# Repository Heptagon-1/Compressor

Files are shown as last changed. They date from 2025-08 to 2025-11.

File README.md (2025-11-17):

# Compressor: Open Source Compound Bow Press
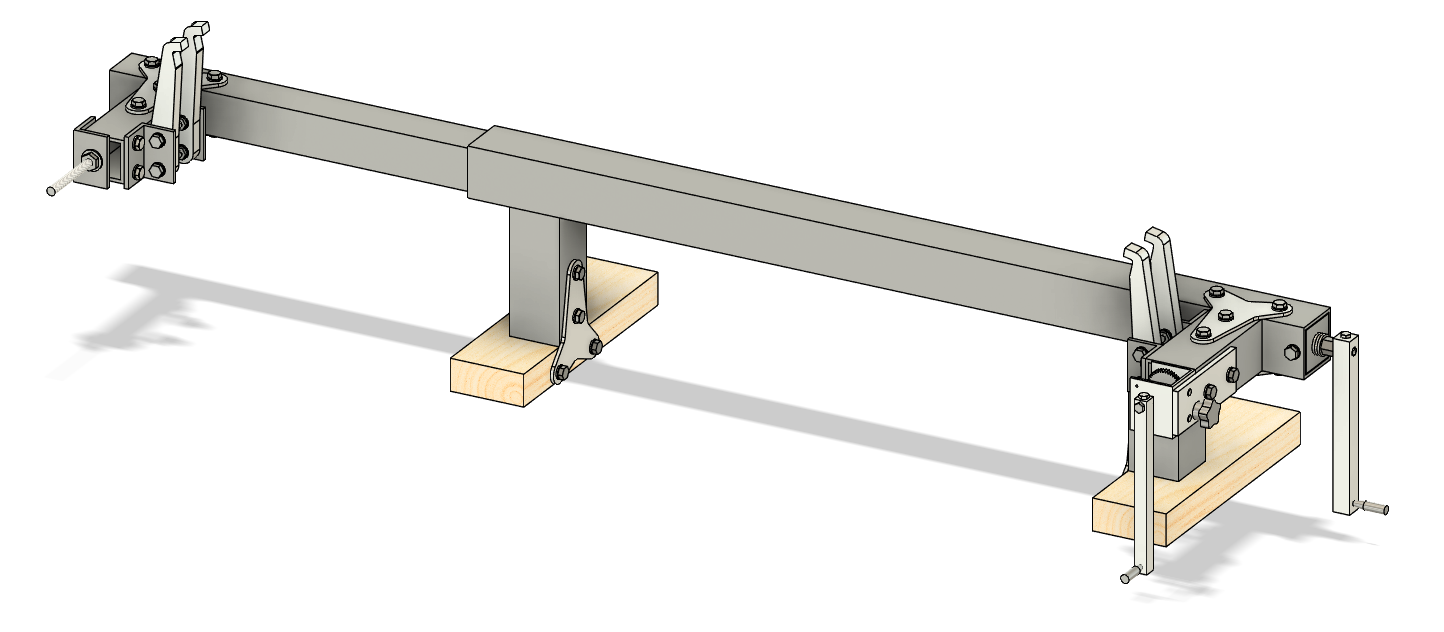
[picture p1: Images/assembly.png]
Assembly


Compressor is a low-cost, highly capable open-source bow press designed to be constructed from commonly available steel and aluminium stock. 
## Features:
- Capable of pressing bows up to 42" AtA.
- Draw board with lock for handsfree use.
- Accommodates split limb bows with a limb gap of more than 12mm (not compatible with past-parallel limbs).
- Parts cost of approximately £250-300.
- No welding required - built entirely using common hand tools.
- Only two custom-made parts - everything else is fabricated from common stock sizes.

## Bill of Materials
⚠️ This list may not be perfect - it is recommended to order a few extra fasteners just in case. 
### Fasteners and Hardware
| Fastener 	| Quantity 	| Notes 	|
|---	|---	|---	|
| M5 nylock nut 	| 4 	| 	|
| M5x22 hex bolt 	| 4 	| 	|
| M5x9 washer 	| 8 	| **Must be reduced diameter 9mm washer (DIN 433).** 	|
| 	| 	| 	|
| M6 nylock nut 	| 1 	| 	|
| M6 washer 	| 3 	| 	|
| M6x10 hex bolt 	| 1 	| 	|
| M6x22 hex bolt 	| 1 	| 	|
| M6x35 star knob 	| 1 	| [Example](https://www.accu.co.uk/threaded-clamping-knobs/588655-HHW-M6-40-35-2-PA) 	|
| M6x85 plain hex bolt 	| 1 	| Plain hex bolt, **not** full threaded. Unthreaded section ~67mm required. 	|
| M6 free-spinning handle 	| 2 	| [Example](https://www.vital-parts.co.uk/m6-x-15mm-x-55mm-rotating-nylon--bzp-cylindrical-threaded-handle---male-40202-p.asp). Alternatively this can be 3D printed, in which case an additional M6x70 plain **socket-head** bolt and m6x22 hex bolt will be required for each handle. STL is available [here](/Manufacturing%20files/Rotating_handle.stl). If buying them, ensure at the thread length is at least 10mm. 	|
| 	| 	| 	|
| M8 thin nut 	| 4 	| 	|
| M8 washer 	| 64 	| 	|
| M8x10 hex bolt 	| 30 	| 	|
| M8x12 hex bolt 	| 14 	| 	|
| M8x30 hex bolt 	| 8 	| 	|
| M8x50 flat point grub screw 	| 2 	| Flat point is important. Get slotted drive rather than hex if possible. 	|
| 8x50mm coach screw 	| 4 	| 	|
| 	| 	| 	|
| M10 thin nut 	| 1 	| 	|
| M10 washer 	| 2 	| 	|
| M10x100 hex bolt 	| 1 	| Must be full threaded **not** plain. 	|
| 	| 	| 	|
| TR10x2 1000mm leadscrew 	| 1 	| Should be right-hand thread, 2mm lead. 	|
| TR10x2 flanged brass leadscrew nut 	| 1 	| Right hand thread, 2mm lead. Check it matches the leadscrew thread. 	|
| TR10x2 steel hex leadscrew nut 	| 2 	| Same as above. 	|
### Raw Materials
#### Steel
Steel box sections formed by extrusion often have a seam that protrudes into the inside of the tube, and is impossible to remove without specialised tools. Check with your supplier that this seam is not so prominent that the 50mm square section cannot comfortably fit inside of the 60mm section otherwise you **will not be able to assemble the press**. 
| Stock type 	| Dimensions 	| Quantity 	| Notes 	|
|---	|---	|---	|---	|
| Square box section 	| 60x60mm, 4mm thickness, 1000mm length 	| 1 	| 	|
| 	| 60x60mm, 4mm thickness, 149mm length  	| 3 	| 	|
| 	| 	| 	| 	|
| 	| 50x50mm, 4mm thickness, 480mm length  	| 1 	| 	|
| 	| 50x50mm, 4mm thickness, 154mm 	| 1 	| 	|
| 	| 	| 	| 	|
| Equal angle 90° section 	| 40x40, 5mm thickness, 60mm length 	| 5 	| 	|
| 	| 	| 	| 	|
| C-channel 	| 50x50mm, 3mm thickness, 50mm length 	| 1 	| 	|
| 	| 40x40mm, 3mm thickness, 40mm length 	| 1 	| 	|
#### Aluminium
| Stock type 	| Dimensions 	| Quantity 	| Notes 	|
|---	|---	|---	|---	|
| Flat bar 	| 2" x 1/4", length = ~130mm 	| 1 	| Steel is sold in metric but a lot of aluminium still seems to be imperial for some reason. 	|
| 	| 	| 	| 	|
| C-channel  	| 2" x 2" x 1/8", length = 60mm 	| 1 	| 	|
| 	| 	| 	| 	|
| Square bar 	| 15x15mm, length=200mm 	| 1 	| 	|
| 	| 20x20mm, length=200mm 	| 1 	| 	|
### Custom Manufactured Parts
These are the only parts of the project that need to be custom-made. Various CNC and waterjet companies are available - if you shop around you should be able to get them made for approximately £100. I have had good experiences with Xometry. A referral link to sign up is available [here](https://get.xometry.uk/r/0f2031980c). DXF / STEP files are available in [Manufacturing files](/Manufacturing%20files).
| Part 	| Quantity 	| CAD File 	| Notes 	|
|---	|---	|---	|---	|
| T-bracket 	| 8 	| [Here](/Manufacturing%20files/T%20Bracket.dxf)	| 4mm thickness. Any aluminium grade. 	|
| Limb finger 	| 4 	| [Here](/Manufacturing%20files/Finger.step)	| Any aluminium grade. 	|
### Other
| Part 	| Quantity 	| Notes 	| 	|
|---	|---	|---	|---	|
| Carabiner 	| 1 	| Ensure this is load-rated for at least the poundage of your bow, ideally at least 3x for safety. 	| 	|
| Paracord 	| 1000mm 	| For the draw board - ensure the strength is sufficient for your bow. 	| 	|
| 40 tooth Mod1 6mm bore gear 	| 1 	| [Example](https://www.gearsandsprockets.co.uk/mod-1-40-tooth-tbot-steel-model-gear.html). Ensure your gear has set screws to clamp to the shaft, or be prepared to drill and tap them. 	| 	|
| Electrical tape 	| 	| 	| 	|
| A4 craft foam sheet 	| 	| 	| 	|
| 2" x 4" timber, length = 300mm 	| 2 	| Dimensions are not critical. Wooden feet stop the press from scratching the surface it sits on. 	| 	|
## Tools Used
- Flat file
- Round file
- Hacksaw
- Cordless drill, common drill bit sizes and cutting fluid
	- Drill bit list TBC
- M6 and M8 taps
- Marking out tools
- Adjustable spanner
- Socket set

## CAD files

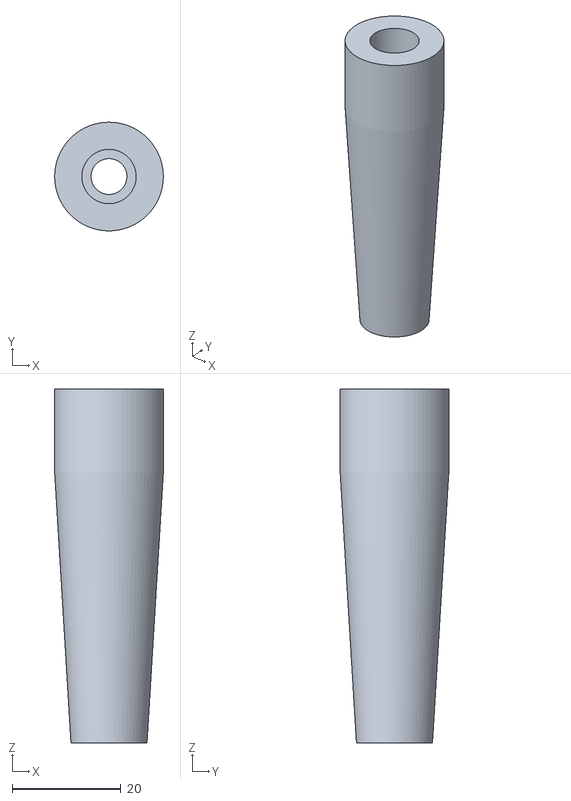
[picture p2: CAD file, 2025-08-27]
Manufacturing files/Rotating_handle.stl
20.0 x 20.0 x 65.1

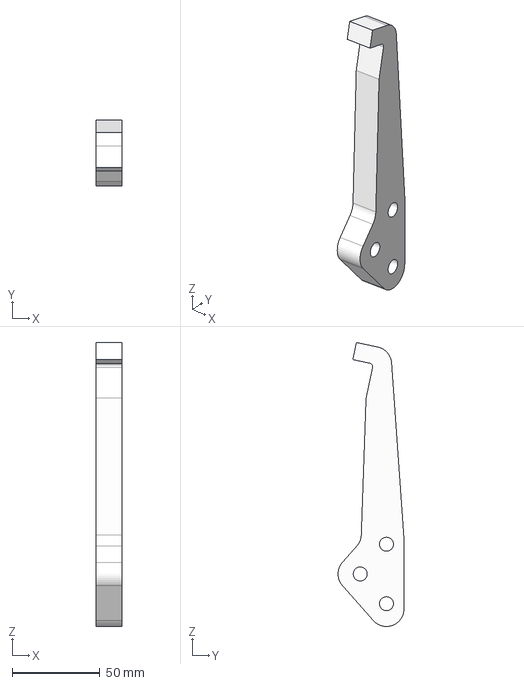
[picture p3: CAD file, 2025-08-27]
Manufacturing files/Finger.step
15.0 x 37.7 x 162.3 mm

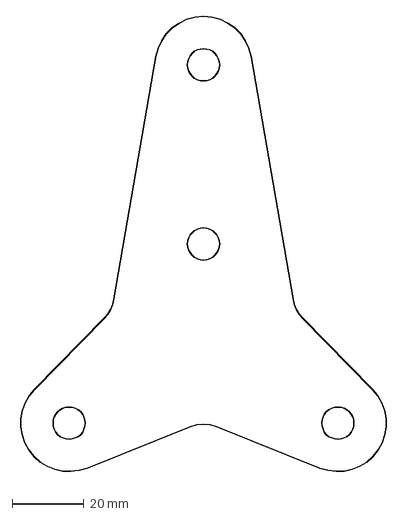
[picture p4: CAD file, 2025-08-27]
Manufacturing files/T Bracket.dxf
104.5 x 128.4 mm

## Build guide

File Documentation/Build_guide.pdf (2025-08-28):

# Build Guide

Some notes before starting:
- This build is designed to be made using hand tools so it doesn’t require any particularly tight tolerances, if everything is within +/-1mm there shouldn’t be any major issues. A couple of areas require slightly finer tolerance than this to make sure things fit together, and these are called out specifically.
- There is quite a lot of drilling and tapping to do in this project. Investing in some decent quality drill bits and cutting fluid will make life a lot easier. I built this using a cordless drill – access to a bench drill isn’t a requirement but will make the build a bit easier.
- If you pick and choose your supplier, you shouldn’t need to cut any big pieces of steel to size yourself as most steel suppliers offer a free or cheap cutting service. The only exception to this were the steel c-channel sections in the leadscrew assembly which are a bit too short for most shops to cut, but these are thin enough that a hacksaw does the job.
- If you have any questions or issues that can’t be resolved using the CAD model then please don’t hesitate to contact me or raise a Github issue.

## 1: Leadscrew Assembly

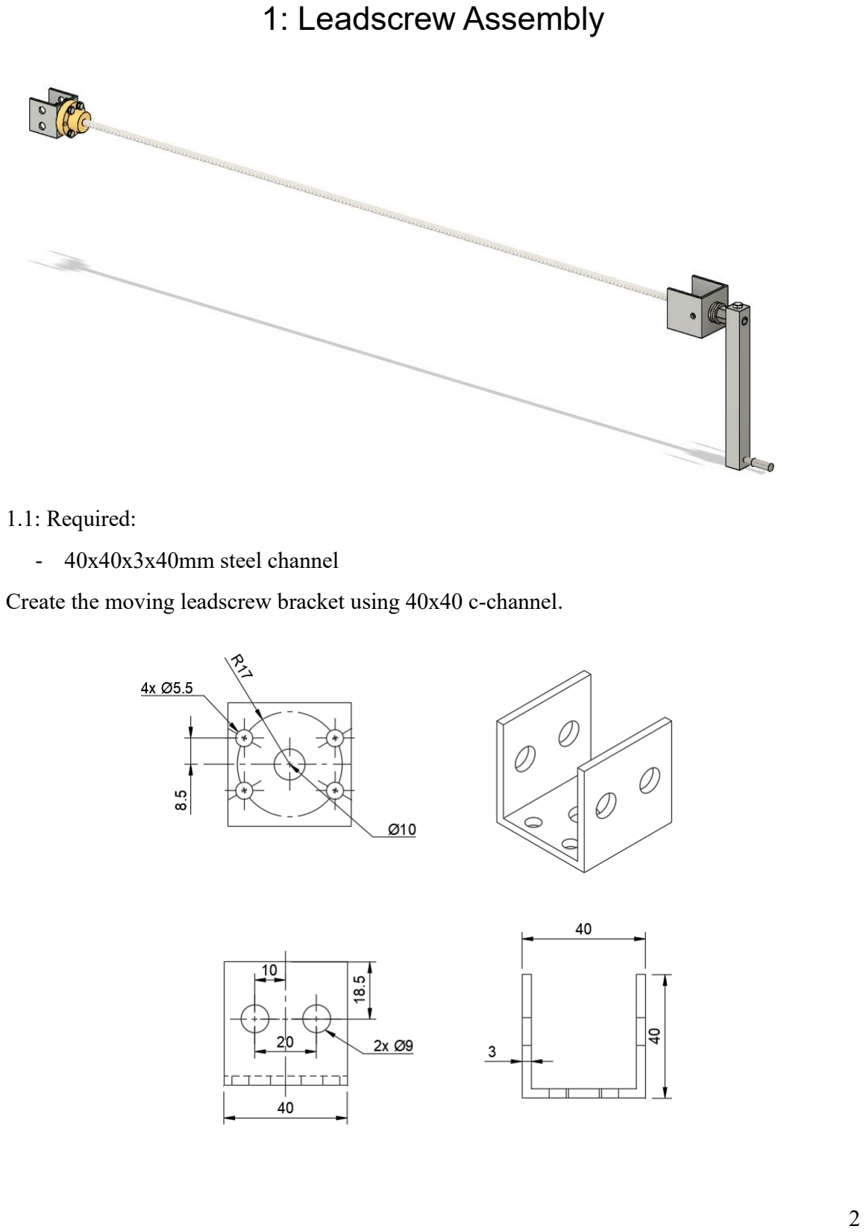
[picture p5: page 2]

1.1: Required:
- 40x40x3x40mm steel channel

Create the moving leadscrew bracket using 40x40 c-channel.

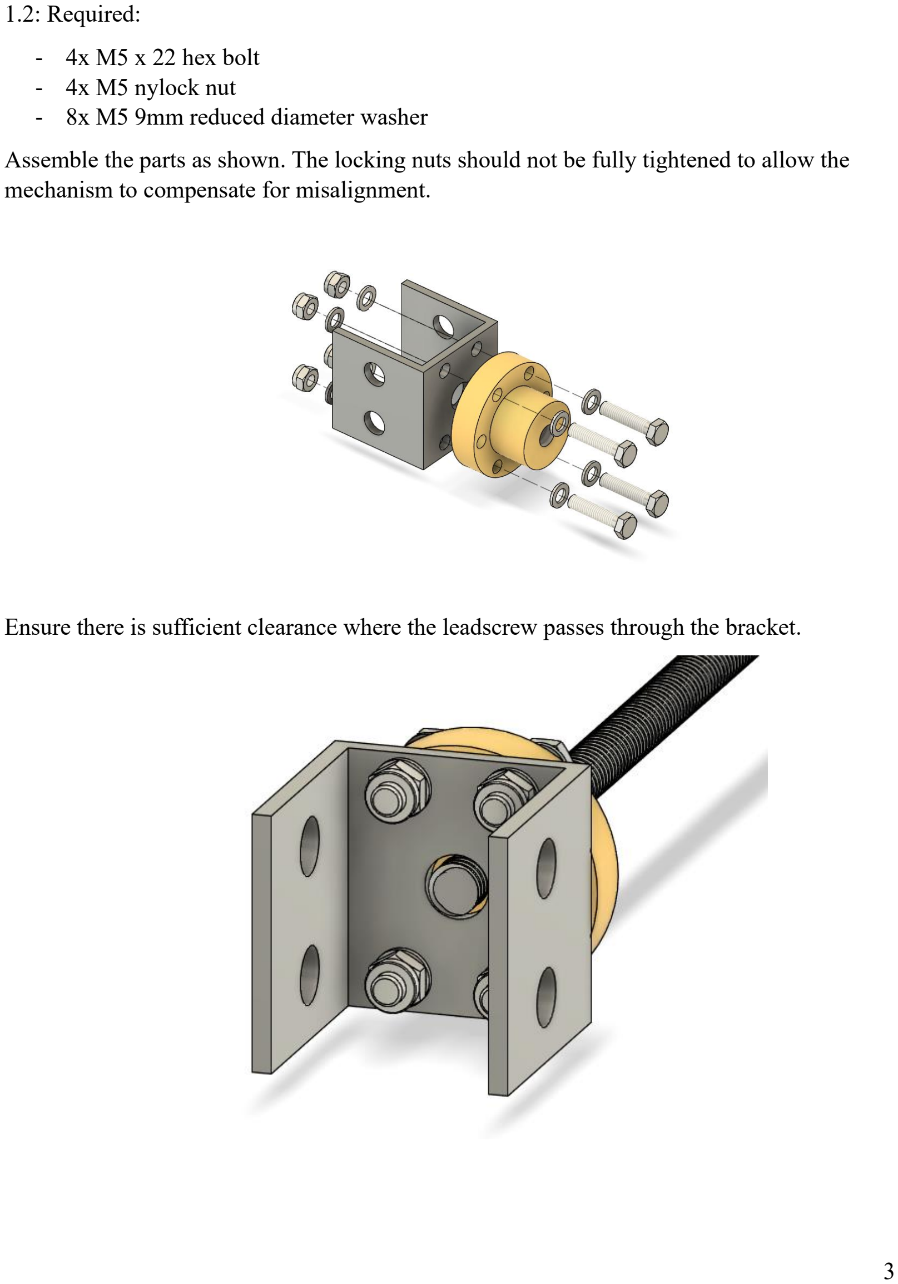
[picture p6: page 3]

1.2: Required:
- 4x M5 x 22 hex bolt
- 4x M5 nylock nut
- 8x M5 9mm reduced diameter washer

Assemble the parts as shown. The locking nuts should not be fully tightened to allow the mechanism to compensate for misalignment.

Ensure there is sufficient clearance where the leadscrew passes through the bracket.

1.3: Required:
- TR10x2 1000mm leadscrew

Prepare the leadscrew by filing a flat on one end. It should extend around 15mm from the end of the screw, and be just deep enough that the threads are not visible in the flat section. Apply some oil to the length of the leadscrew to prevent rust.

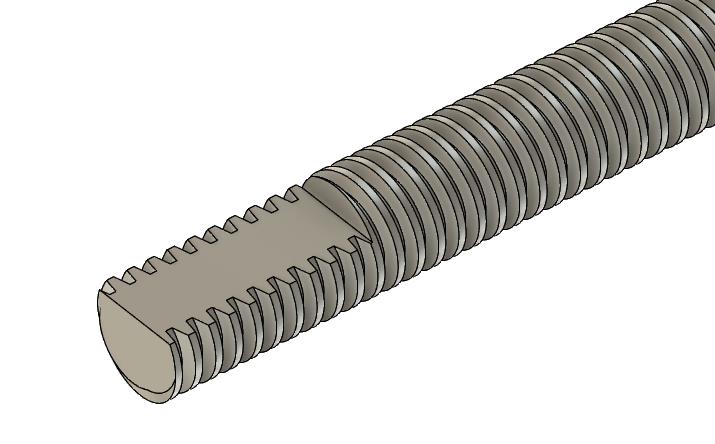
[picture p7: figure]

1.4: Required:
- 20x20x200mm aluminium square bar

Create the handle of the press. If using a 3D printed rotating handle, an additional M6 hole is required on the top. The depth of the threaded holes on the end is not critical so long as they intersect with the holes on the long face.

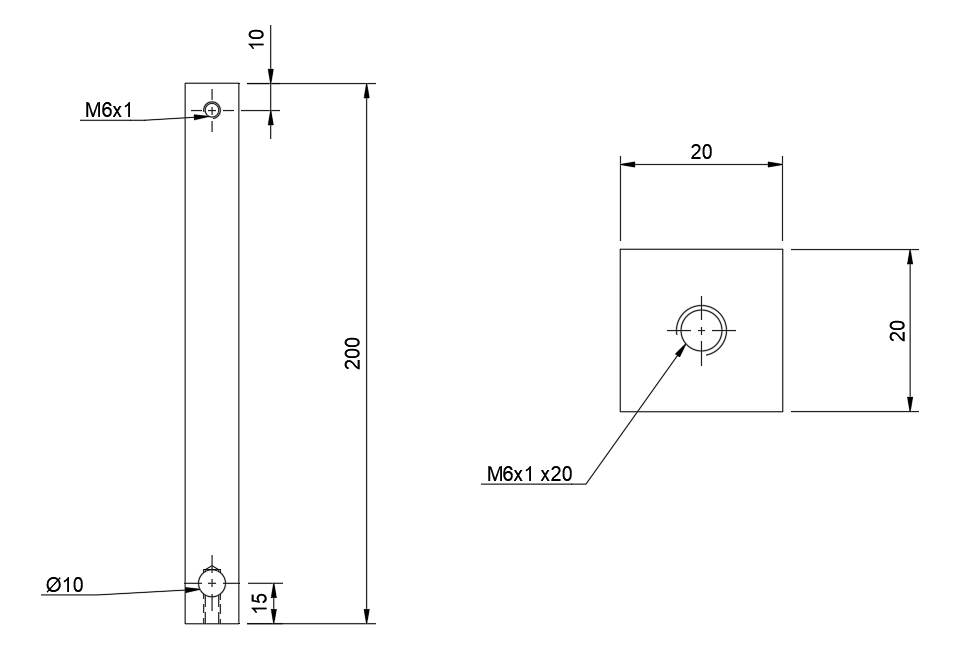
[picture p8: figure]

1.5: Required:
- 50x50x3x50mm steel channel

Create the static leadscrew bracket using the steel channel. Ensure the 10mm hole has sufficient clearance for the leadscrew.

1.6: Required:
- 10mm adjusting ring
- 2x TR10x2 hex leadscrew nut
- 2x 51100 thrust bearing
- Static leadscrew bracket from 1.5
- Leadscrew

Add all of the parts to the leadscrew in the following order:

1. 10mm adjusting ring
2. TR10 hex nut
3. 51100 thrust bearing
4. Static leadscrew bracket
5. 51100 thrust bearing
6. TR10 hex nut

Do not tighten down the adjusting ring yet.

1.7: Required:
- Bow press handle
- M6x22 hex bolt

Attach the handle flush with the end of the leadscrew using the M6 bolt, then move the parts from 1.6 up towards the handle. The bracket should be sandwiched between the two thrust bearings just tightly enough that it cannot rattle. Tighten down the adjusting ring once everything is in place.

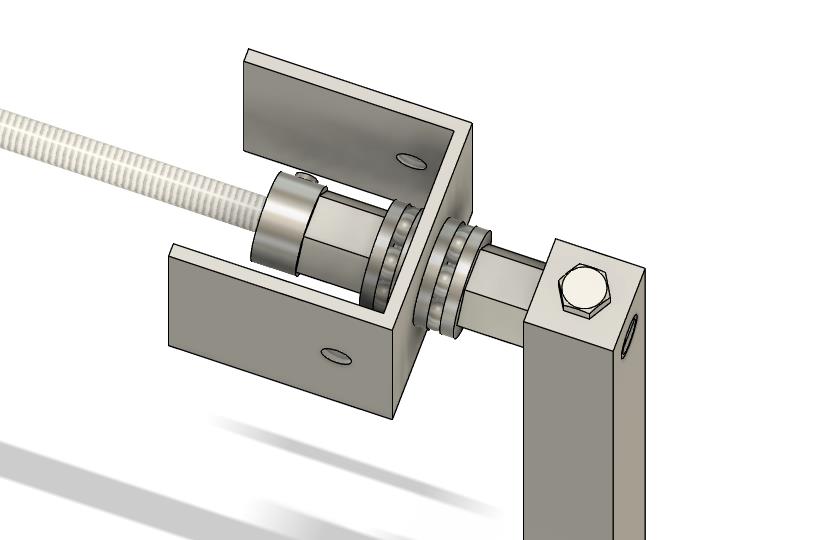
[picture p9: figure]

1.8: Required:
- M6 rotating handle

Attach the free-spinning grip to the end of the handle. If 3D printing the handle instead, lock the bolt in place using the threaded hole you made in the other end.

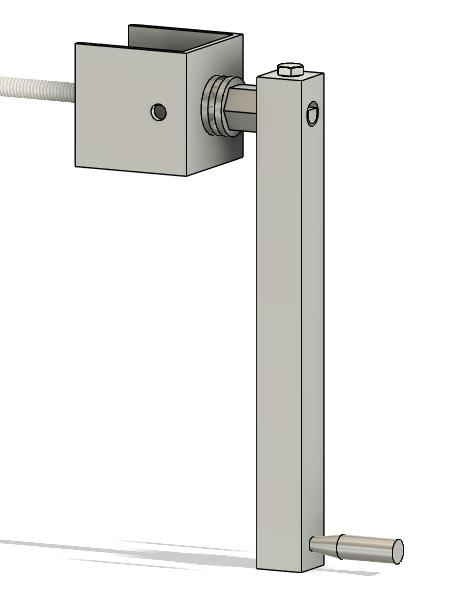
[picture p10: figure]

The leadscrew assembly is now completed.

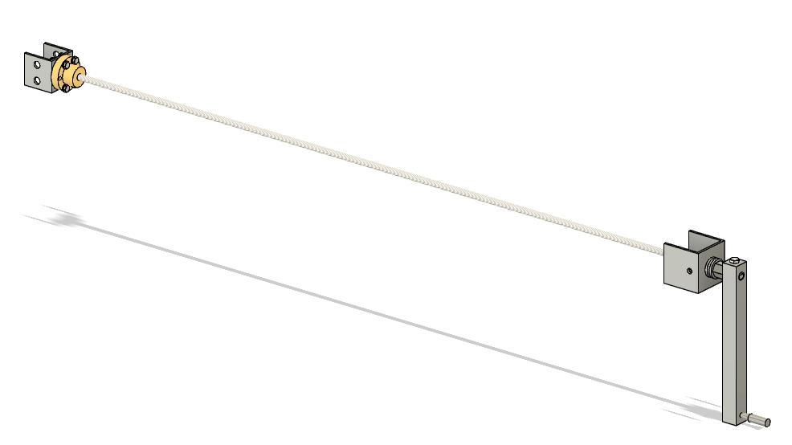
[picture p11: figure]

## 2: Main Mody Assembly

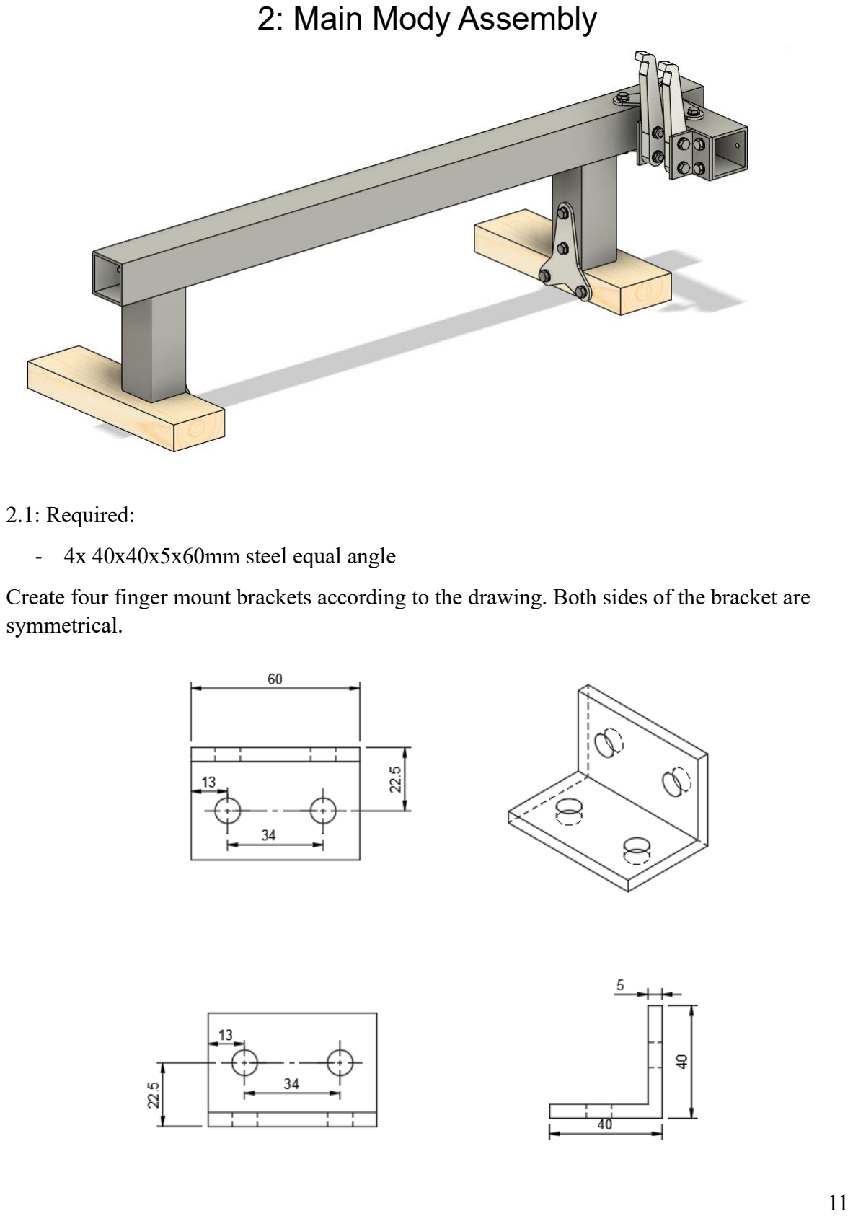
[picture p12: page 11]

2.1: Required:
- 4x 40x40x5x60mm steel equal angle

Create four finger mount brackets according to the drawing. Both sides of the bracket are symmetrical.

2.2: Required:
- 4x Finger mount brackets from 2.1
- 4x Fingers
- 8x M8x30 hex bolts
- 8x M8 thin nuts
- 16x M8 washers

Create four finger assemblies. These are symmetrical – create two left variants and two right variants. Exact alignment of the fingers is not critical right now, this will be adjusted later.

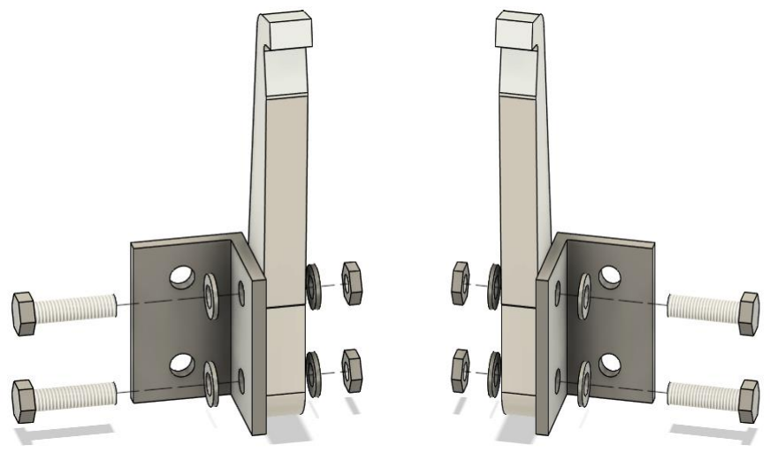
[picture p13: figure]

2.3: Required:
- 60x60x4x1000mm square box section steel

Create the main body of the press. I recommend labelling the top, front, rear and bottom faces of the workpiece first to match the drawings. Note that the hole centreline in the top is 25mm from the front and the line on the rear is 25mm from the bottom. The centreline on the front is in the centre (~30mm from each side). Also note the tolerances on the 25mm dimensions – do not place the holes more than 25mm from the edge, or additional work will be required during assembly

All holes are M8 tapped, except for the 9mm hole through the front and rear faces. Once all hole locations are marked, double check against the drawings and CAD before drilling and tapping any. This is probably the most complex and awkward component in the whole build.

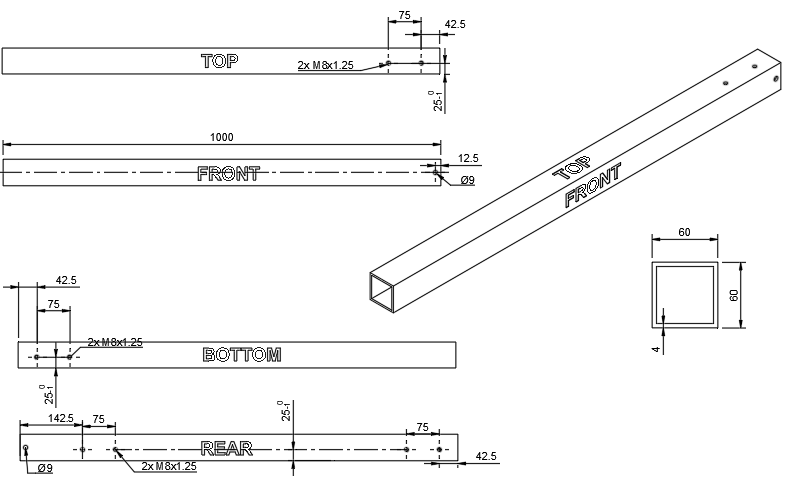
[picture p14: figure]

2.4: Required:
- 2x 60x60x4x149 square box section steel

Create a pair of these which are mirror images. Note the tolerance on the 25mm dimensions. All four holes are M8 tapped.

2.5: Required:
- 60x60x4x149 square box section steel

Create the mount for attaching the fingers. Note the tolerances on some of the dimensions. The distance between the two pairs of holes must be selected to match the gap between your split limbs. The default 107mm value corresponds to PSE Dominator Duo 30mm gap limbs.

Distance between inside limb edges (mm) | Distance value in drawing (mm)
20 | 97
25 | 102
30 (PSE Dominator Duo) | 107

Once the holes are marked, double check against the CAD before drilling. All holes are M8 tapped.

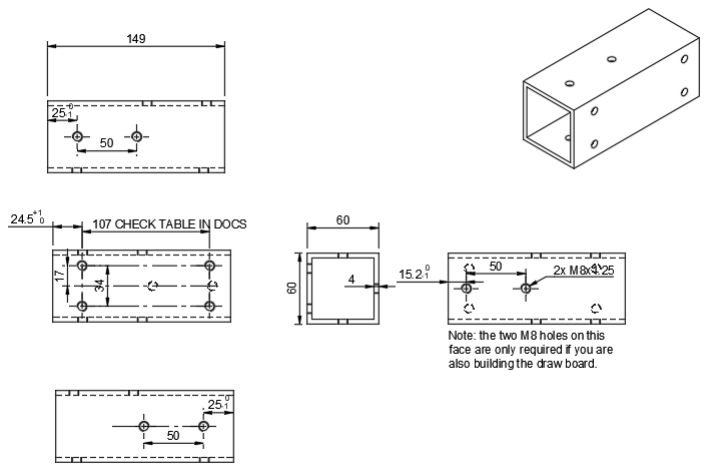
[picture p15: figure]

2.6: Required:
- 2x 2x4” 300mm timber

Drill the pilot holes according to the drawing. Check the required pilot hole diameter and depth for the specific screws you are using. Make two mirrored versions of this.

2.7: Required:
- 14x M8x10 hex bolts
- 4x M8x50 coach screws
- 20x M8 washers
- 4x T-brackets

Assemble the base according to the diagrams.

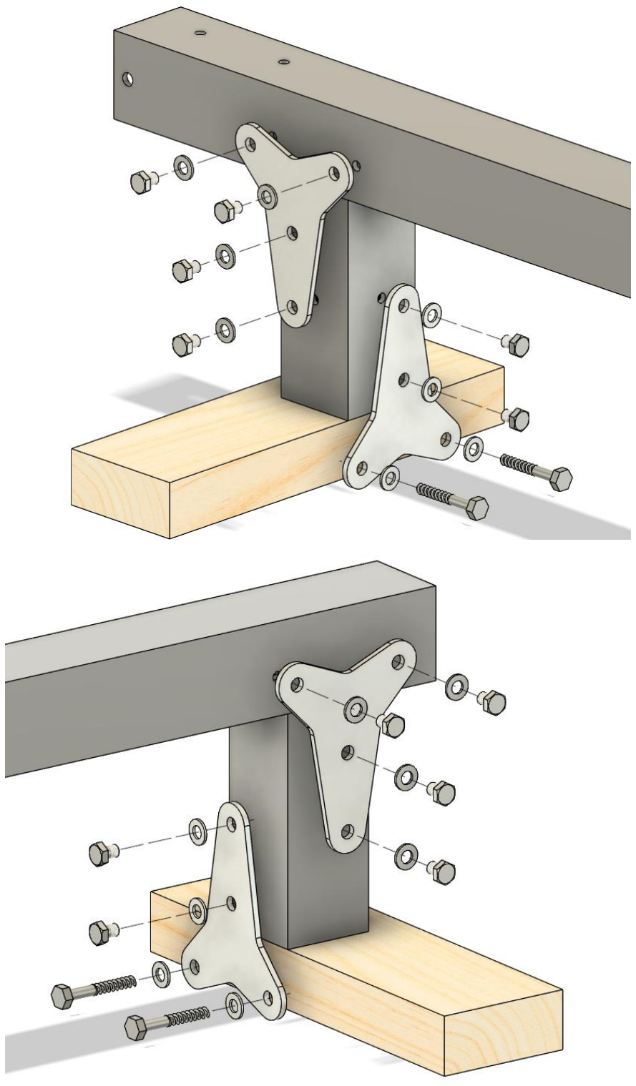
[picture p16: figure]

2.8: Required:
- 4x M8x12 hex bolt
- 4x M8 washers

Attach the fingers to the mount using M8x12 bolts. After, loosen the M8x30 bolts slightly and ensure the fingers are aligned before retightening.

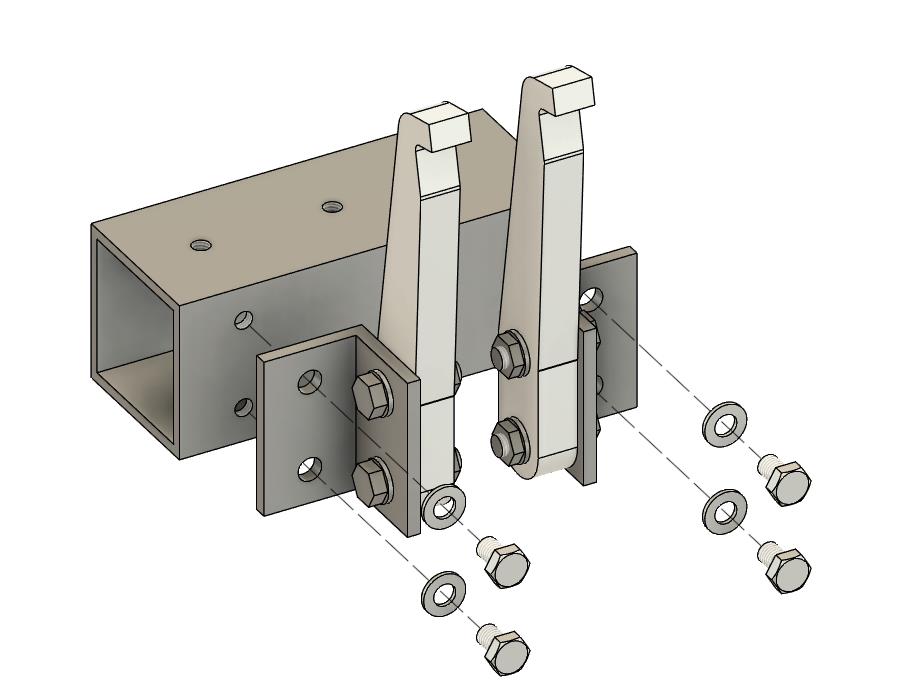
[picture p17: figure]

2.9: Required:
- 8x M8x10 hex bolts
- 8x M8 washers
- 2x T-brackets

Attach the finger assembly to the base using M8x10 bolts.

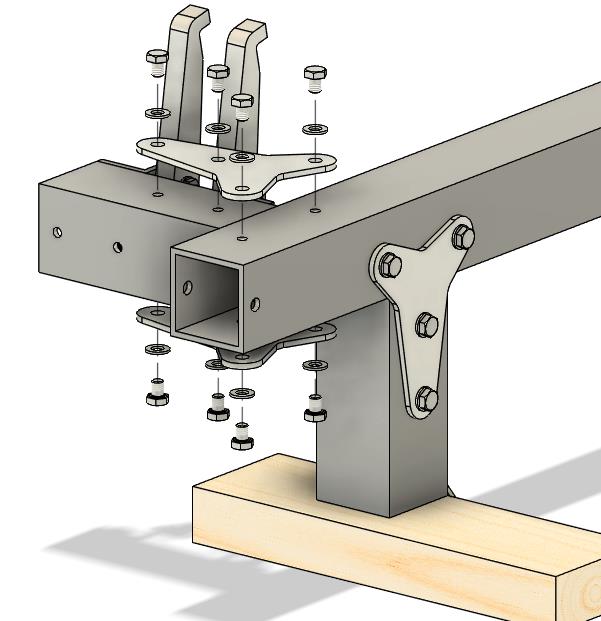
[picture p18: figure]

The main body assembly should is now completed.

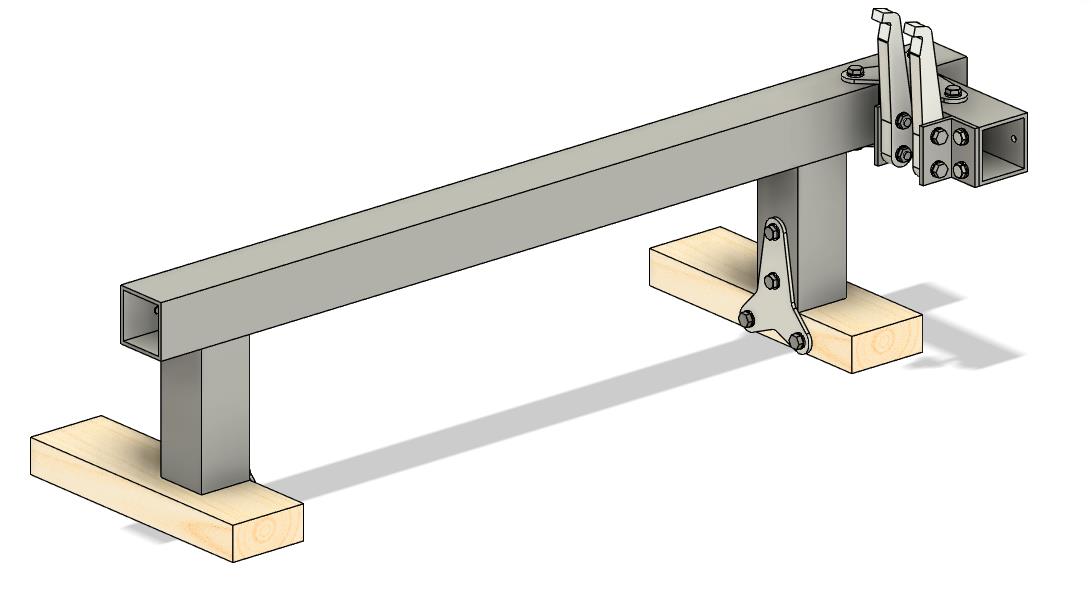
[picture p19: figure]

## 3: Moving Body Section

3.1: Required:
- 50x50x4x480mm square box section steel

This part should be much simpler to make than the long section in the main body. As always, double check the marking out before drilling the holes.

3.2: Required:
- 50x50x4x154mm square box section steel

Take note of the tolerances on some of the dimensions. For the front face with four threaded holes, refer to the limb spacing table from earlier.

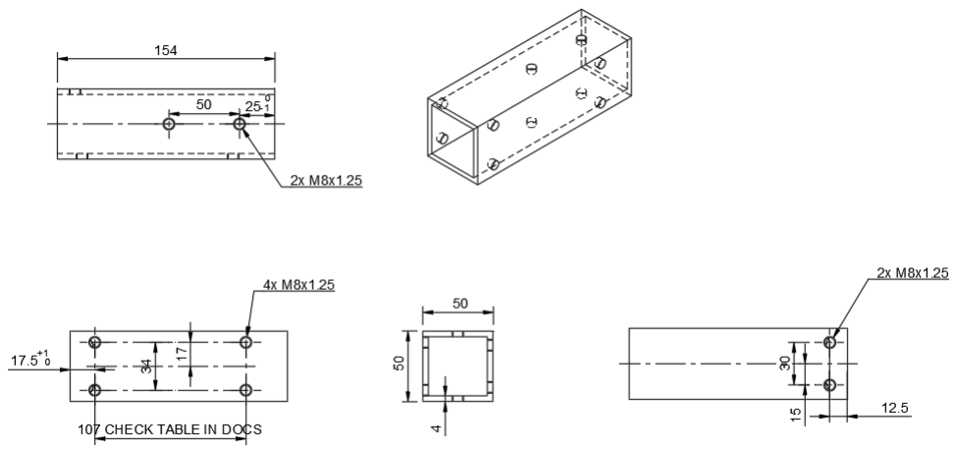
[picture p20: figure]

3.3: Required:
- 4x M8x12 hex bolts
- 4x M8 washers

Attach the fingers to the mount from the previous step. Afterwards, loosen the M8x30 bolts to even out the fingers.

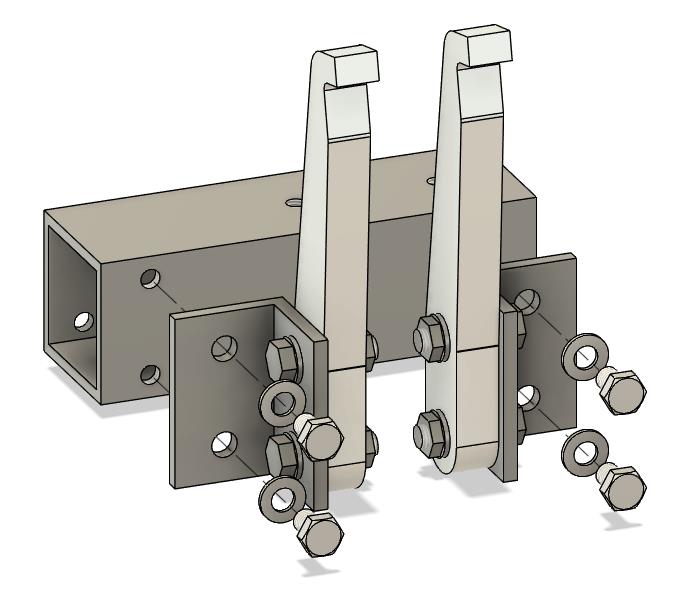
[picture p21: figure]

3.4: Required:
- 8x M8x10 hex bolts
- 8x M8 washers
- 2x T-brackets

Assemble the two parts as shown. A small round file may be needed to enlarge the holes in the T-brackets if hole locations are not perfect.

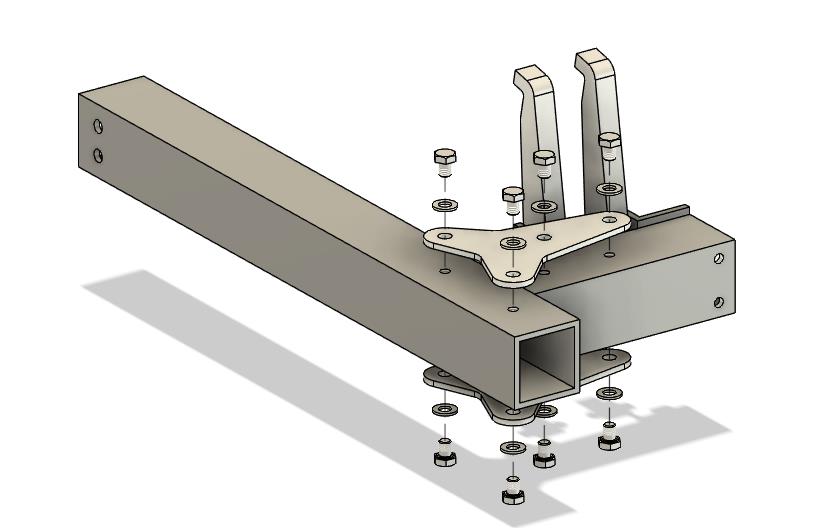
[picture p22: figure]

The moving side of the body is now completed.

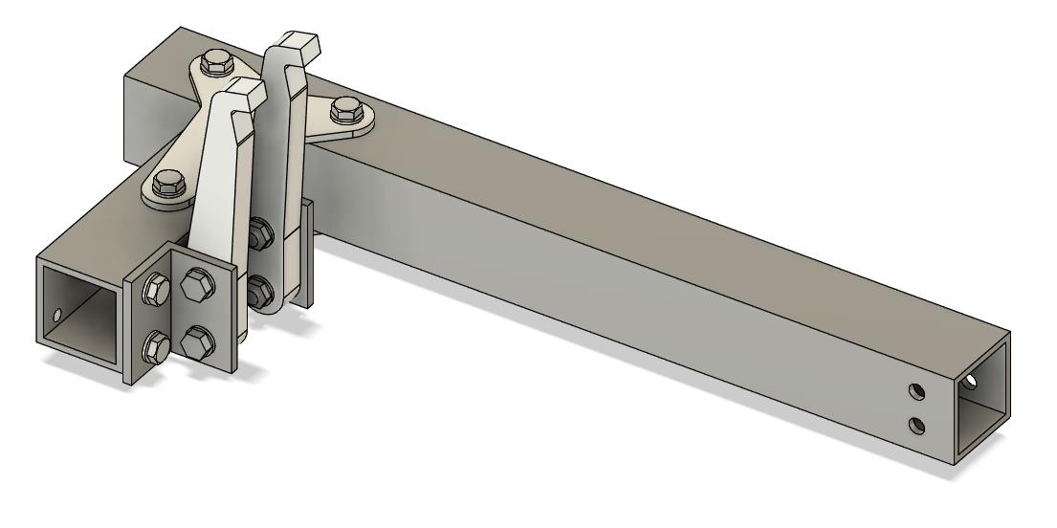
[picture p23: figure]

## 4: Final assembly of the press

4.1: Required:
- 2x M8x50 flat point slotted grub screws

Insert the leadscrew nut assembly into the end of the box section so that the four 9mm holes line up. It may be necessary to file the edges of the c-channel down to account for the radii of the box section corners. Pin it in place using the two grub screws. They will be loose at this stage; they are captured by the main body once the assembly is complete.

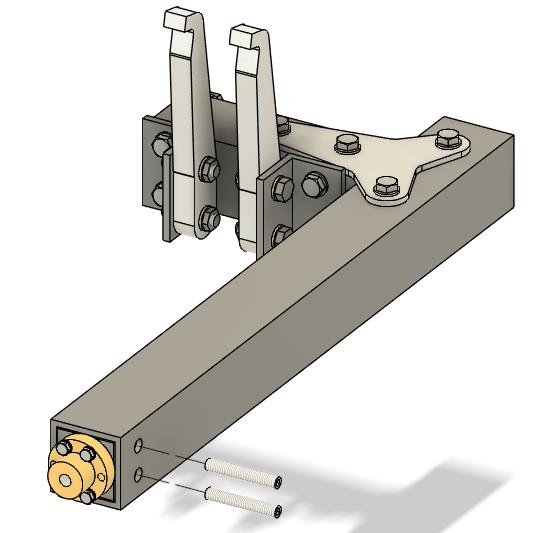
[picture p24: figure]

4.2: Required:
- 2x M8x10 hex bolts
- 2x M8 washers

Insert the handle end of the leadscrew assembly into the main body. It may also need to be filed to account for the corner radii. Secure it in place using the M8 bolts and washers.

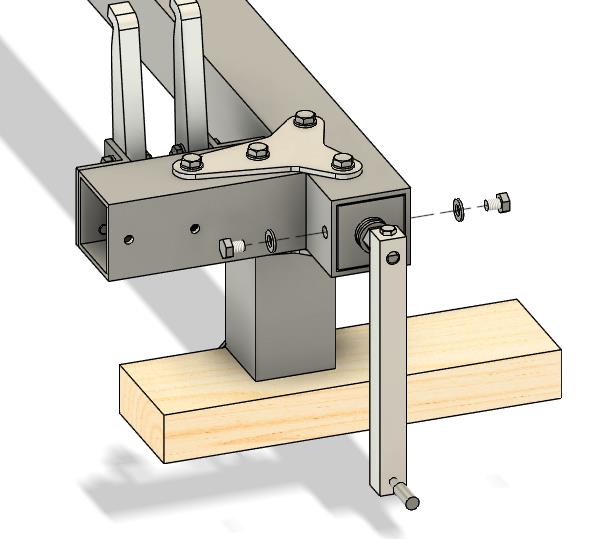
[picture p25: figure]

4.3: Place the moving assembly in the end of the main body, and temporarily remove the highlighted bolt.

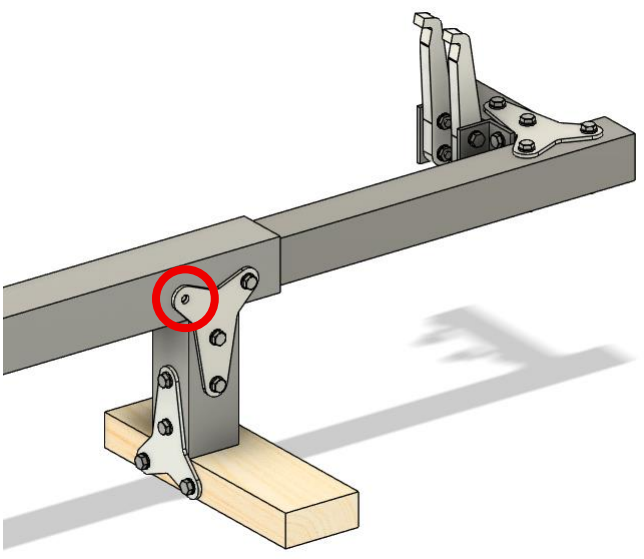
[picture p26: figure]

4.4: Insert an allen key through the bolt hole and lift the leadscrew to align it with the leadscrew nut. Once aligned, thread the leadscrew into the flanged nut.

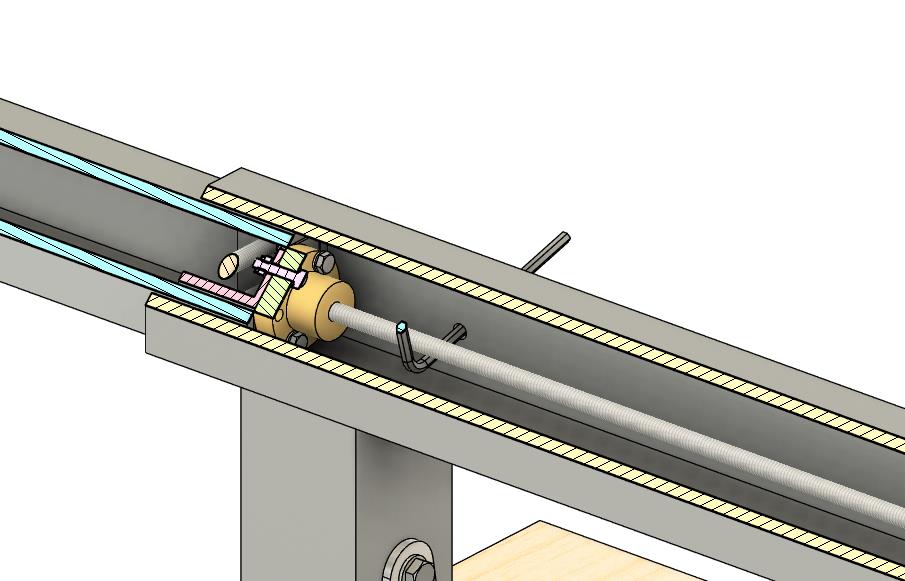
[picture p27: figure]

4.5: Once a few threads of the leadscrew are engaged with the leadscrew nut, make a mark where the base and moving parts meet to avoid extending the press too far in future and needing to realign the leadscrew. Replace the bolt that was removed earlier.

4.6: The basic version of the press is now complete. Before pressing a bow for the first time, test it thoroughly by clamping a piece of timber or equivalent between the fingers and applying a significant force to ensure nothing slips under load.

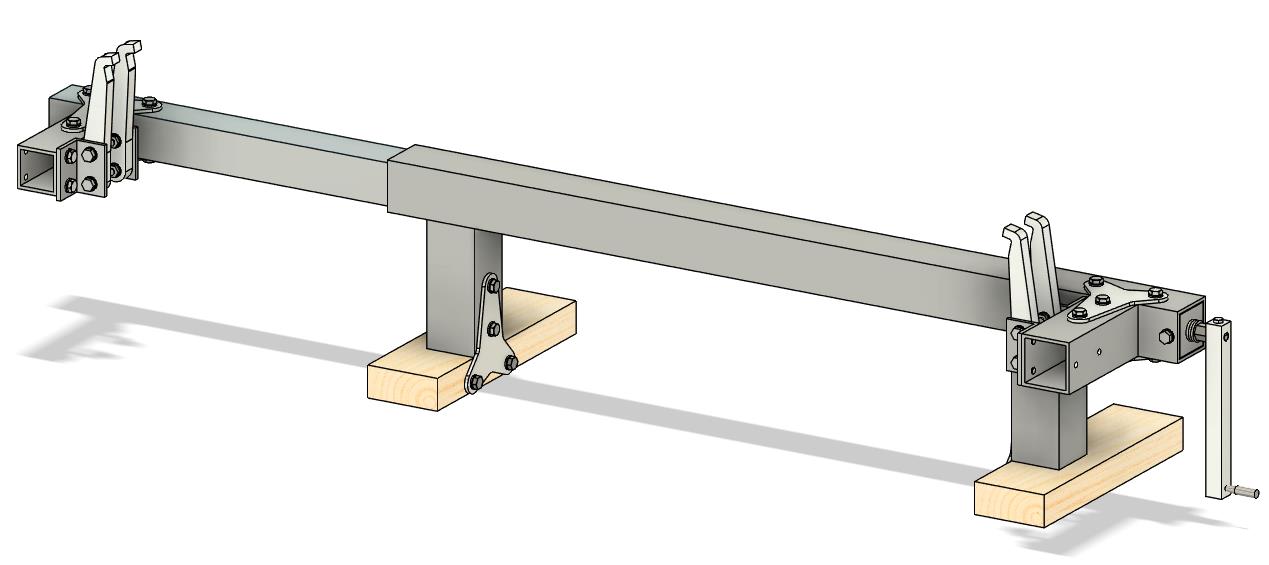
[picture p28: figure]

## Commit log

2025-08-27 Started writing up BOM and readme and added CAD files.
    [Finger.step, T Bracket.dxf]
2025-08-27 Updated CAD to consistently use shop-bought M6 handles rather than 3D printed ones and matched BOM. Added note about 3D printing handles as alternative.
    [Rotating_handle.stl]
2025-08-27 Fixed missing links to CAD files in readme.
2025-08-27 Added image and switched readme links to relative format
2025-08-28 Adjusted leg design to reduce separate part count. Modelled d-shape on the leadscrew. Added missing handle stock material to the BOM.
2025-08-28 Started writing assembly guide, fixed missing numbers in readme
2025-08-28 Completed instructions for press without draw board
2025-08-28 Updated CAD model
